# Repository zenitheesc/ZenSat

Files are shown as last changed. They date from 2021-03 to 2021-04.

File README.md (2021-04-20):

<h1 align="center" style="color:white; background-color:black">ZenSat</h1>
<h4 align="center">This is an Open Hardware and Software CubeSat developed by Zenith EESC-USP for the CubeDesign 2018.</h4>

<p align="center">
	<a href="http://zenith.eesc.usp.br/">
    
    </a>
    <a href="https://eesc.usp.br/">
    
    </a>
    <a href="https://github.com/zenitheesc/USPSat-AE1/blob/main/LICENSE">
    
    </a>
    <a href="https://github.com/zenitheesc/USPSat-AE1/issues">
    
    </a>
    <a href="https://github.com/zenitheesc/USPSat-AE1/commits/main">
    
    </a>
    <a href="https://github.com/zenitheesc/USPSat-AE1/graphs/contributors">
    
    </a>
    <a href="https://github.com/zenitheesc/USPSat-AE1/commits/main">
    
    </a>
    <a href="https://github.com/zenitheesc/USPSat-AE1/issues">
    
    </a>
    <a href="https://github.com/zenitheesc/USPSat-AE1/pulls">
    
    </a>
</p>

Aiming to participate in the first CubeDesign in 2018, Zenith designed its first nanosatellite prototype, which was named ”ZenSat”. This project was a 2U CubeSat for imaging missions in the competition. It is worth mentioning that the focus of the project was not to validate a nanosatellite for flight but to enable a first contact between the group members and the development of a nanosatellite.

<p align = "center">
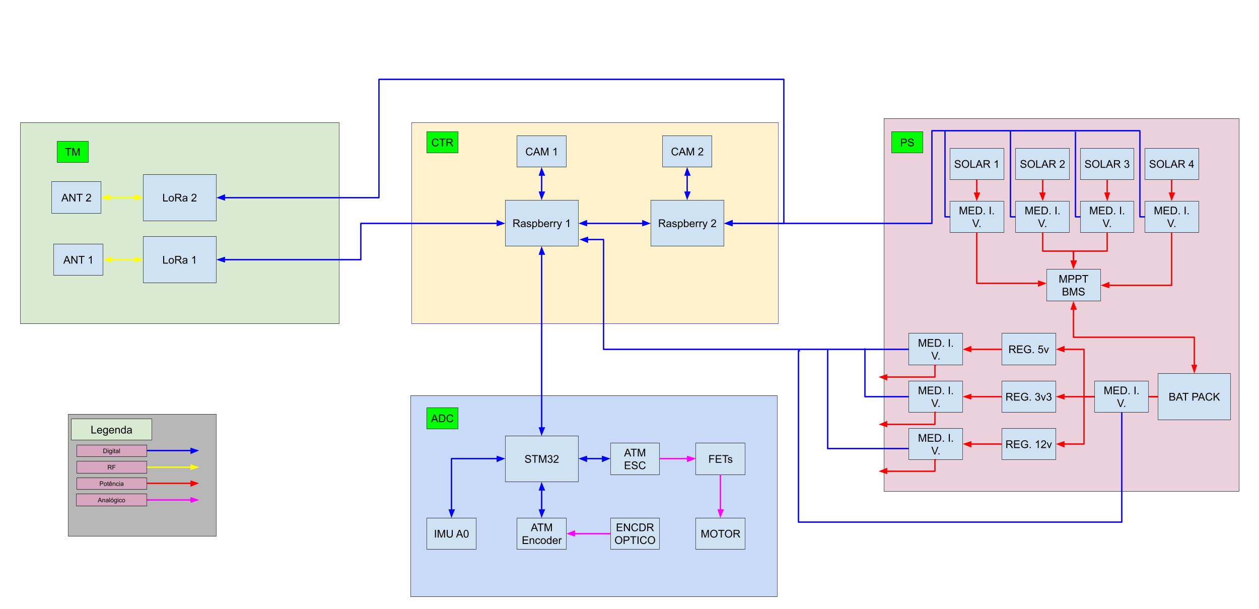
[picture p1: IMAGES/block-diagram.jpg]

</p>

<a href="https://github.com/zenitheesc/ZenSat_1.0/tree/master/ADC%20-%20Attitude%20Determination%20and%20Control"><h2> ADC - Attitude Determination and Control </h2></a>
The entire stabilization and pointing system must be done necessary to fulfill the competition missions. For this, the reading is done necessary sensors, activating a reaction wheel, which, by means of the Law of Conservation of Angular Momentum, manages to act in the attitude of the satellite.

<p align = "center">
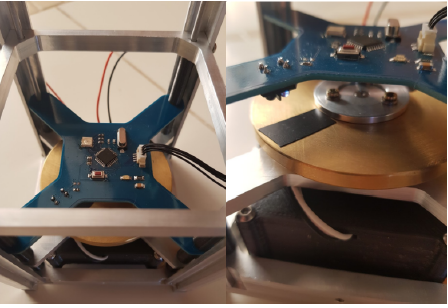
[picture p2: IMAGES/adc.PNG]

</p>

<a href="https://github.com/zenitheesc/ZenSat_1.0/tree/master/COM%20-%20Command%20and%20Telemetry"><h2>COM - Command and Telemetry</h2></a>
It is responsible by the bidirectional telemetry in cubesat. This System has two LoRa radios, which communicate with the CTRL Subsystem

<p align = "center">
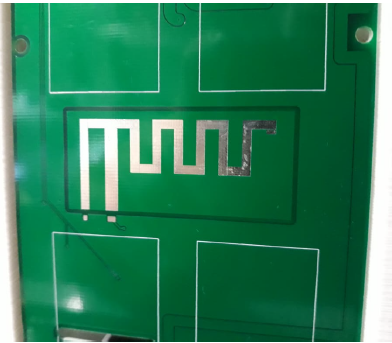
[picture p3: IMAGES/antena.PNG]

</p>

<a href="https://github.com/zenitheesc/ZenSat_1.0/tree/master/COM%20-%20Command%20and%20Telemetry"><h2>CTRL - Control</h2></a>
The Control System is the main component of the project. This system is responsible for data analysis, decision making and controlling the others systems
<p align = "center">
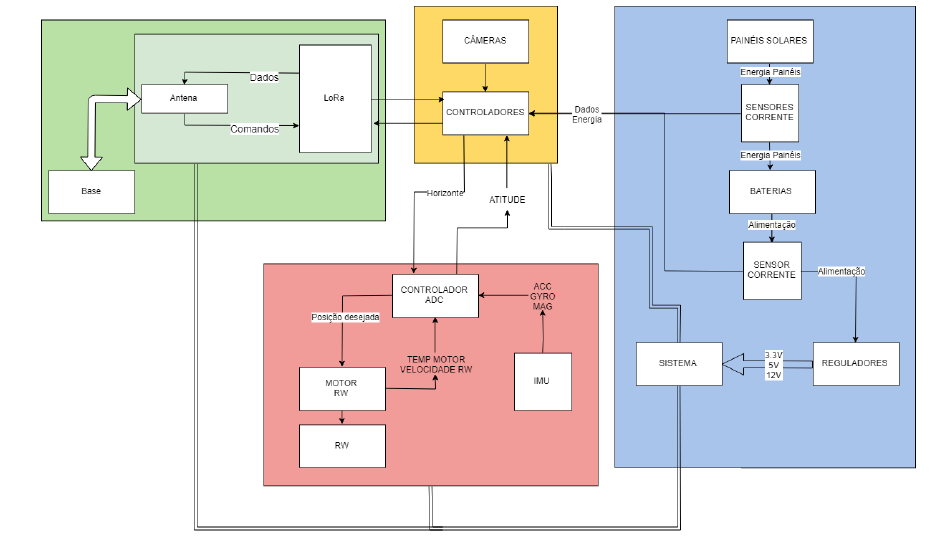
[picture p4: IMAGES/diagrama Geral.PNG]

</p>

<a href="https://github.com/zenitheesc/ZenSat_1.0/tree/master/PS%20-%20Power%20Supply"><h2>PS - Power Supply</h2></a>
Ensures the monitoring and control of EPS panel parameters,
that is, it performs the measurement of voltage and current levels at various points on the CubeSat;
monitors the temperature of the batteries and acts to keep it always positive, in addition to
carry out communication with other subsystems.
Also it performs conversions of battery voltage levels to the levels requested within the
hardware, making the necessary distribution, as well as controlling the loading of batteries through solar panels.

<p align = "center">
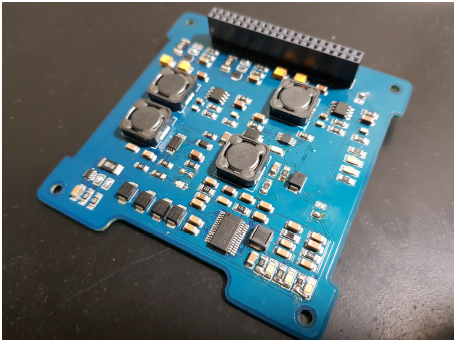
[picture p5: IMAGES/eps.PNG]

</p>

<a href="https://github.com/zenitheesc/ZenSat_1.0/tree/master/STT%20-%20Structure"><h2> STT - Structure </h2></a>
Finally, we have the subsystem responsible for the physical integration of all
the subsystems described earlier. All manufacturing issues involving
the physical structure of ZenSat is the responsibility of the structures subsystem. The
determination of the materials used, the choice of manufacturing processes and display of all components, aiming at a satisfactory performance in the
vibration, are the main focuses of this subsystem

<p align = "center">
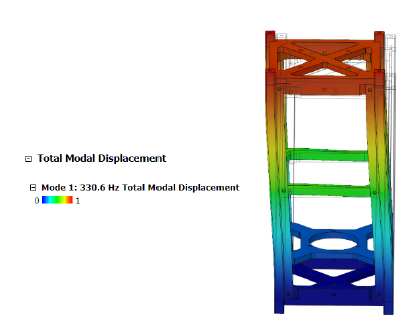
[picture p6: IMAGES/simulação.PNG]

</p>

## Official Documentation

Check out the official documentation [here](https://github.com/zenitheesc/ZenSat_1.0/blob/master/ZenSat%20v.1.0.pdf).

<p align = "center">
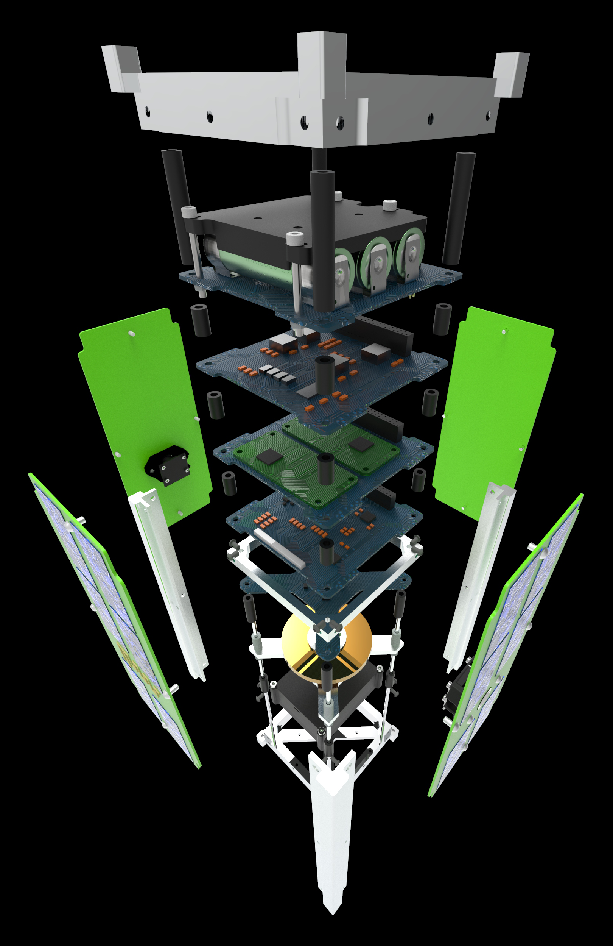
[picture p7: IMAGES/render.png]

</p>

<p align="center">
    <a href="http://zenith.eesc.usp.br">
    
    </a> 
    <a href="https://www.facebook.com/zenitheesc">
    
    </a> 
    <a href="https://www.instagram.com/zenith_eesc/">
    
    </a>

</p>
<p align = "center">
<a href="zenith.eesc@gmail.com">zenith.eesc@gmail.com</a>
</p>

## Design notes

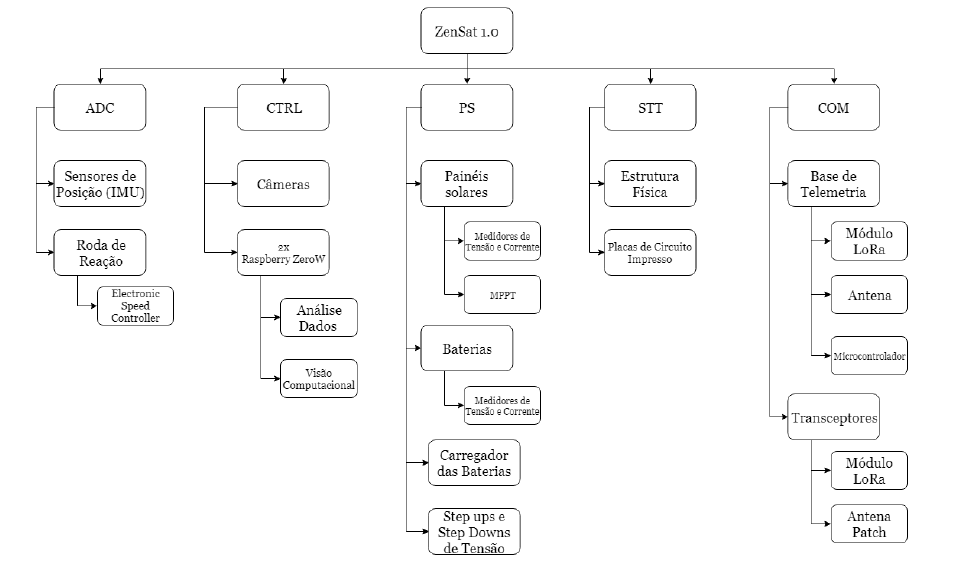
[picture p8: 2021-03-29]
IMAGES/breakdown.PNG

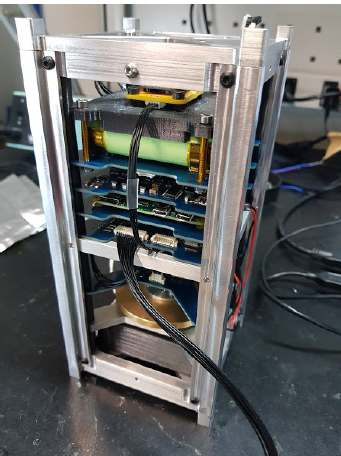
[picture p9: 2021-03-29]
IMAGES/aberto.PNG

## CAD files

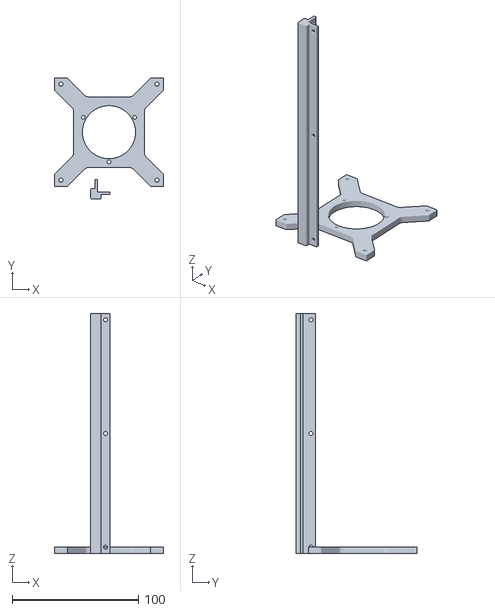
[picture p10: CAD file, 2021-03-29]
STT - Structure/trilho suporte motor.stl
86.0 x 96.0 x 190.0

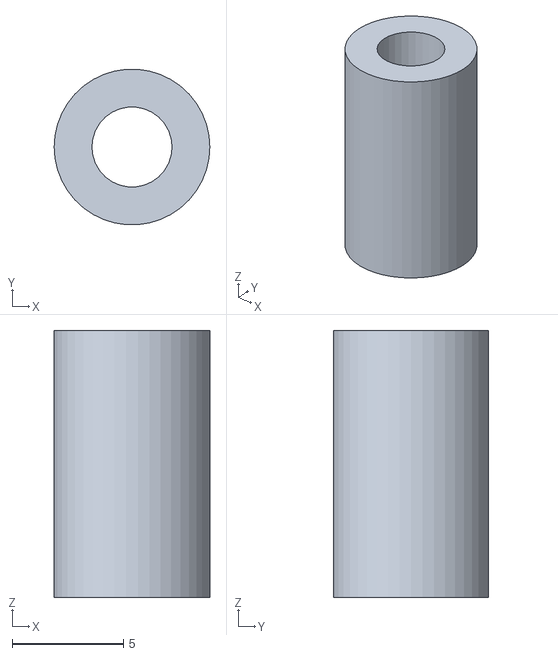
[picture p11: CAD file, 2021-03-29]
STT - Structure/espacador4.stl
7.00 x 6.98 x 12.0

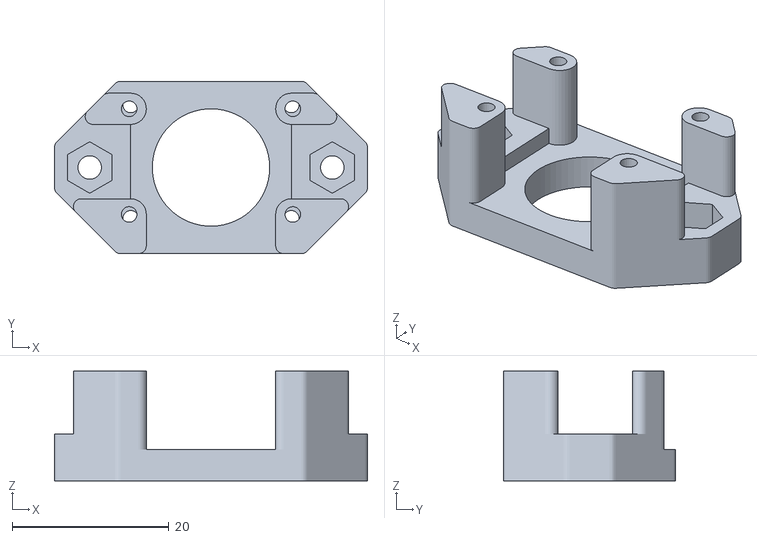
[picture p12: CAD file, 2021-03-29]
STT - Structure/suporte camera 2.0.stl
40.0 x 22.0 x 14.0

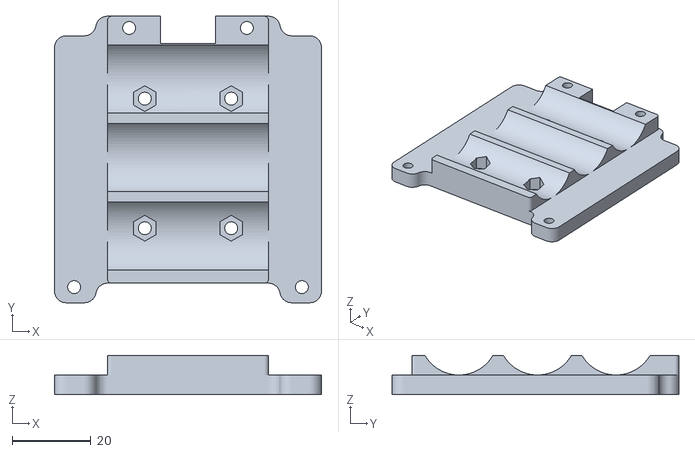
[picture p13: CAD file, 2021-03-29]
STT - Structure/suporte-baterias.stl
68.0 x 73.0 x 10.0

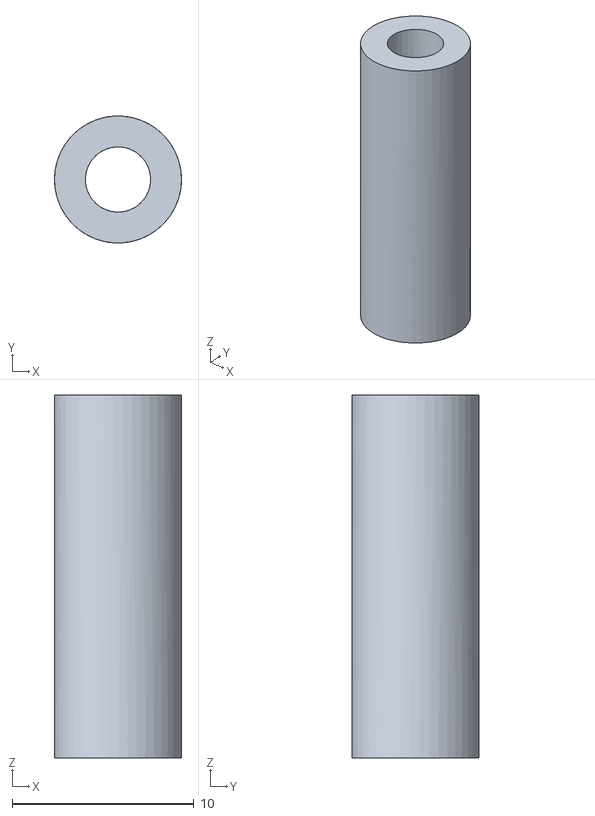
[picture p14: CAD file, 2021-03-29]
STT - Structure/espacador_1.stl
7.00 x 7.00 x 20.0

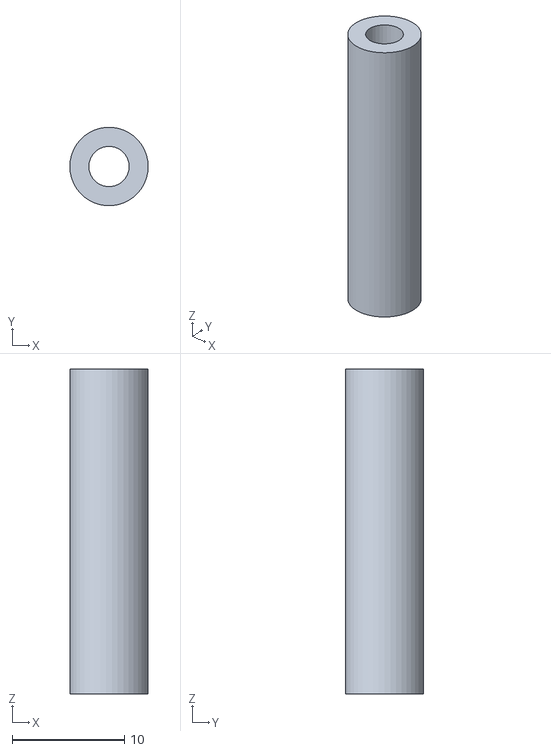
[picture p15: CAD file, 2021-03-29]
STT - Structure/espaçador3,6.stl
7.00 x 6.98 x 29.0

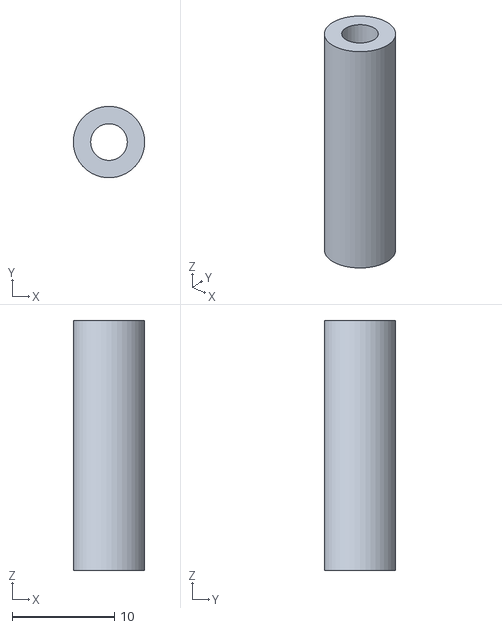
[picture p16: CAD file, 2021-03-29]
STT - Structure/espacador2.stl
7.00 x 6.99 x 24.5

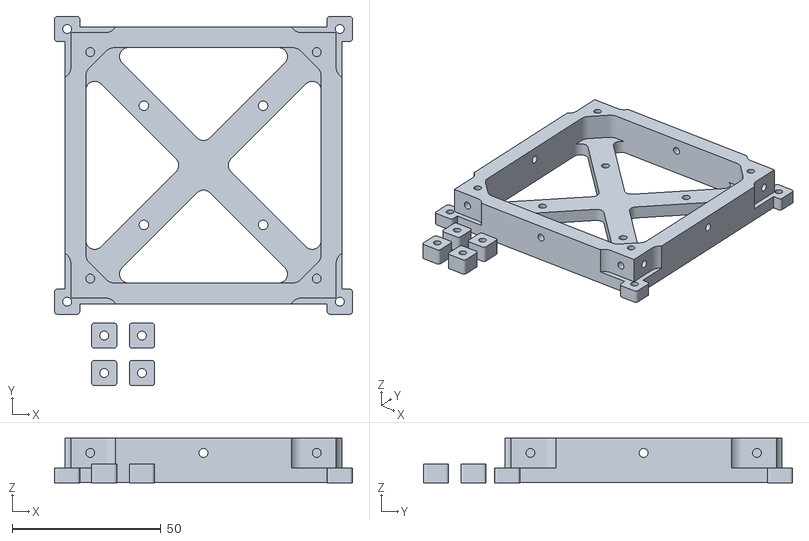
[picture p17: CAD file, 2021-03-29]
STT - Structure/tampa2_slice.stl
100.0 x 123.9 x 15.1

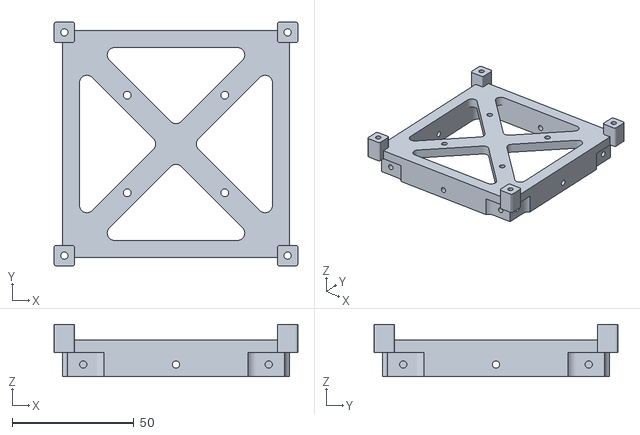
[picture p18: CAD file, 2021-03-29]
STT - Structure/tampa2.stl
100.0 x 100.0 x 21.5

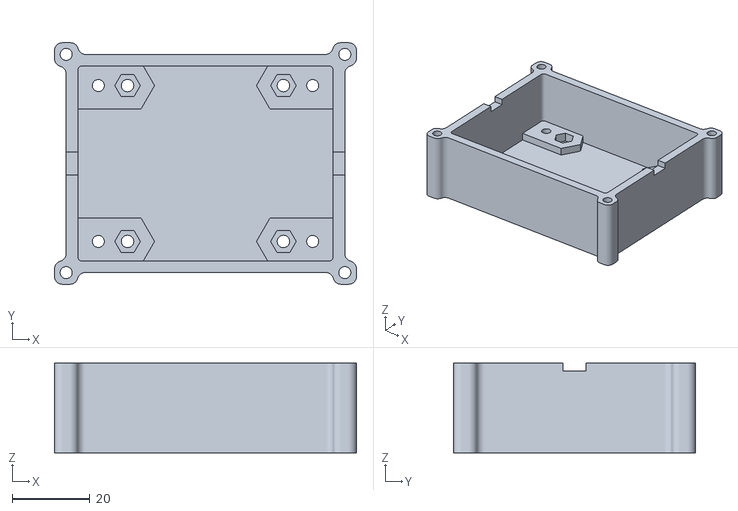
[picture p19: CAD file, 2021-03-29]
STT - Structure/caixa_esc.stl
77.5 x 62.0 x 23.0

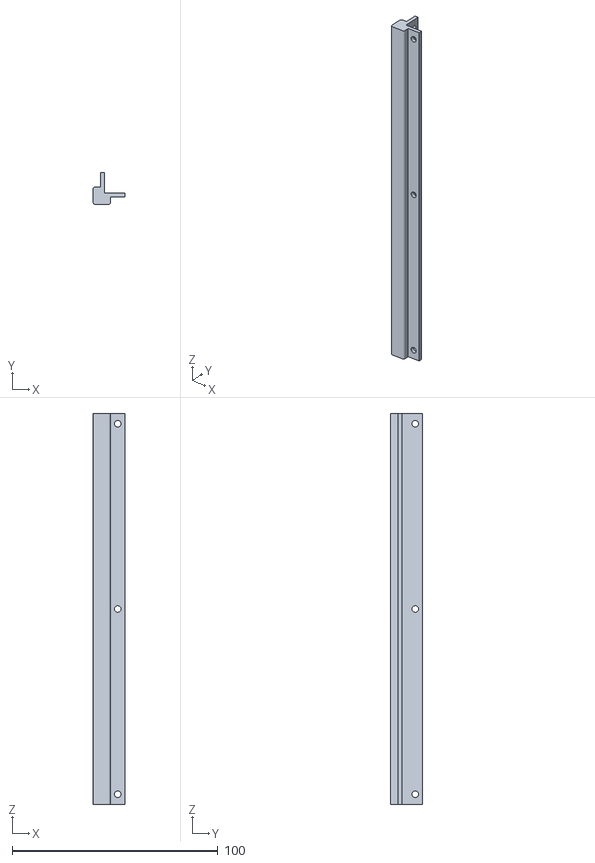
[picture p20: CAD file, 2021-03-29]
STT - Structure/trilho v2.0.stl
15.5 x 15.5 x 190.0

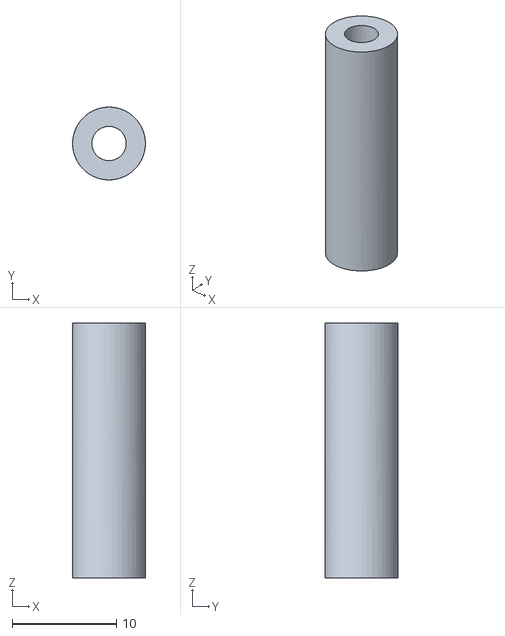
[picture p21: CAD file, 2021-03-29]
STT - Structure/espaçador_2.stl
7.00 x 7.00 x 24.5

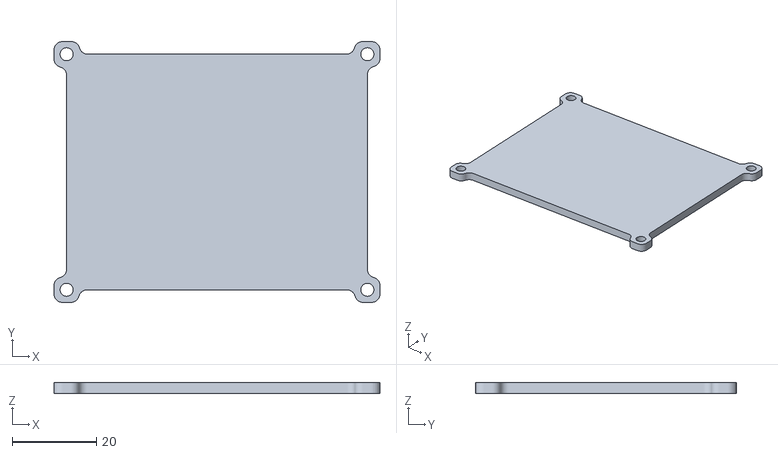
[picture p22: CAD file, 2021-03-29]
STT - Structure/tampa_esc.stl
77.5 x 62.0 x 2.50

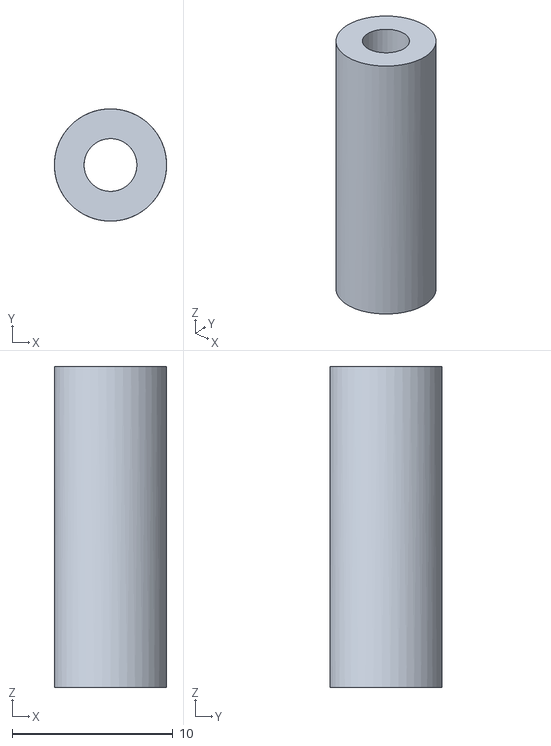
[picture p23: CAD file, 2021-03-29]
STT - Structure/espaçador_1.stl
7.00 x 7.00 x 20.0

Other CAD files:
STT - Structure/espacador 3.stl
STT - Structure/espacador5.stl
STT - Structure/suporte roda.stl

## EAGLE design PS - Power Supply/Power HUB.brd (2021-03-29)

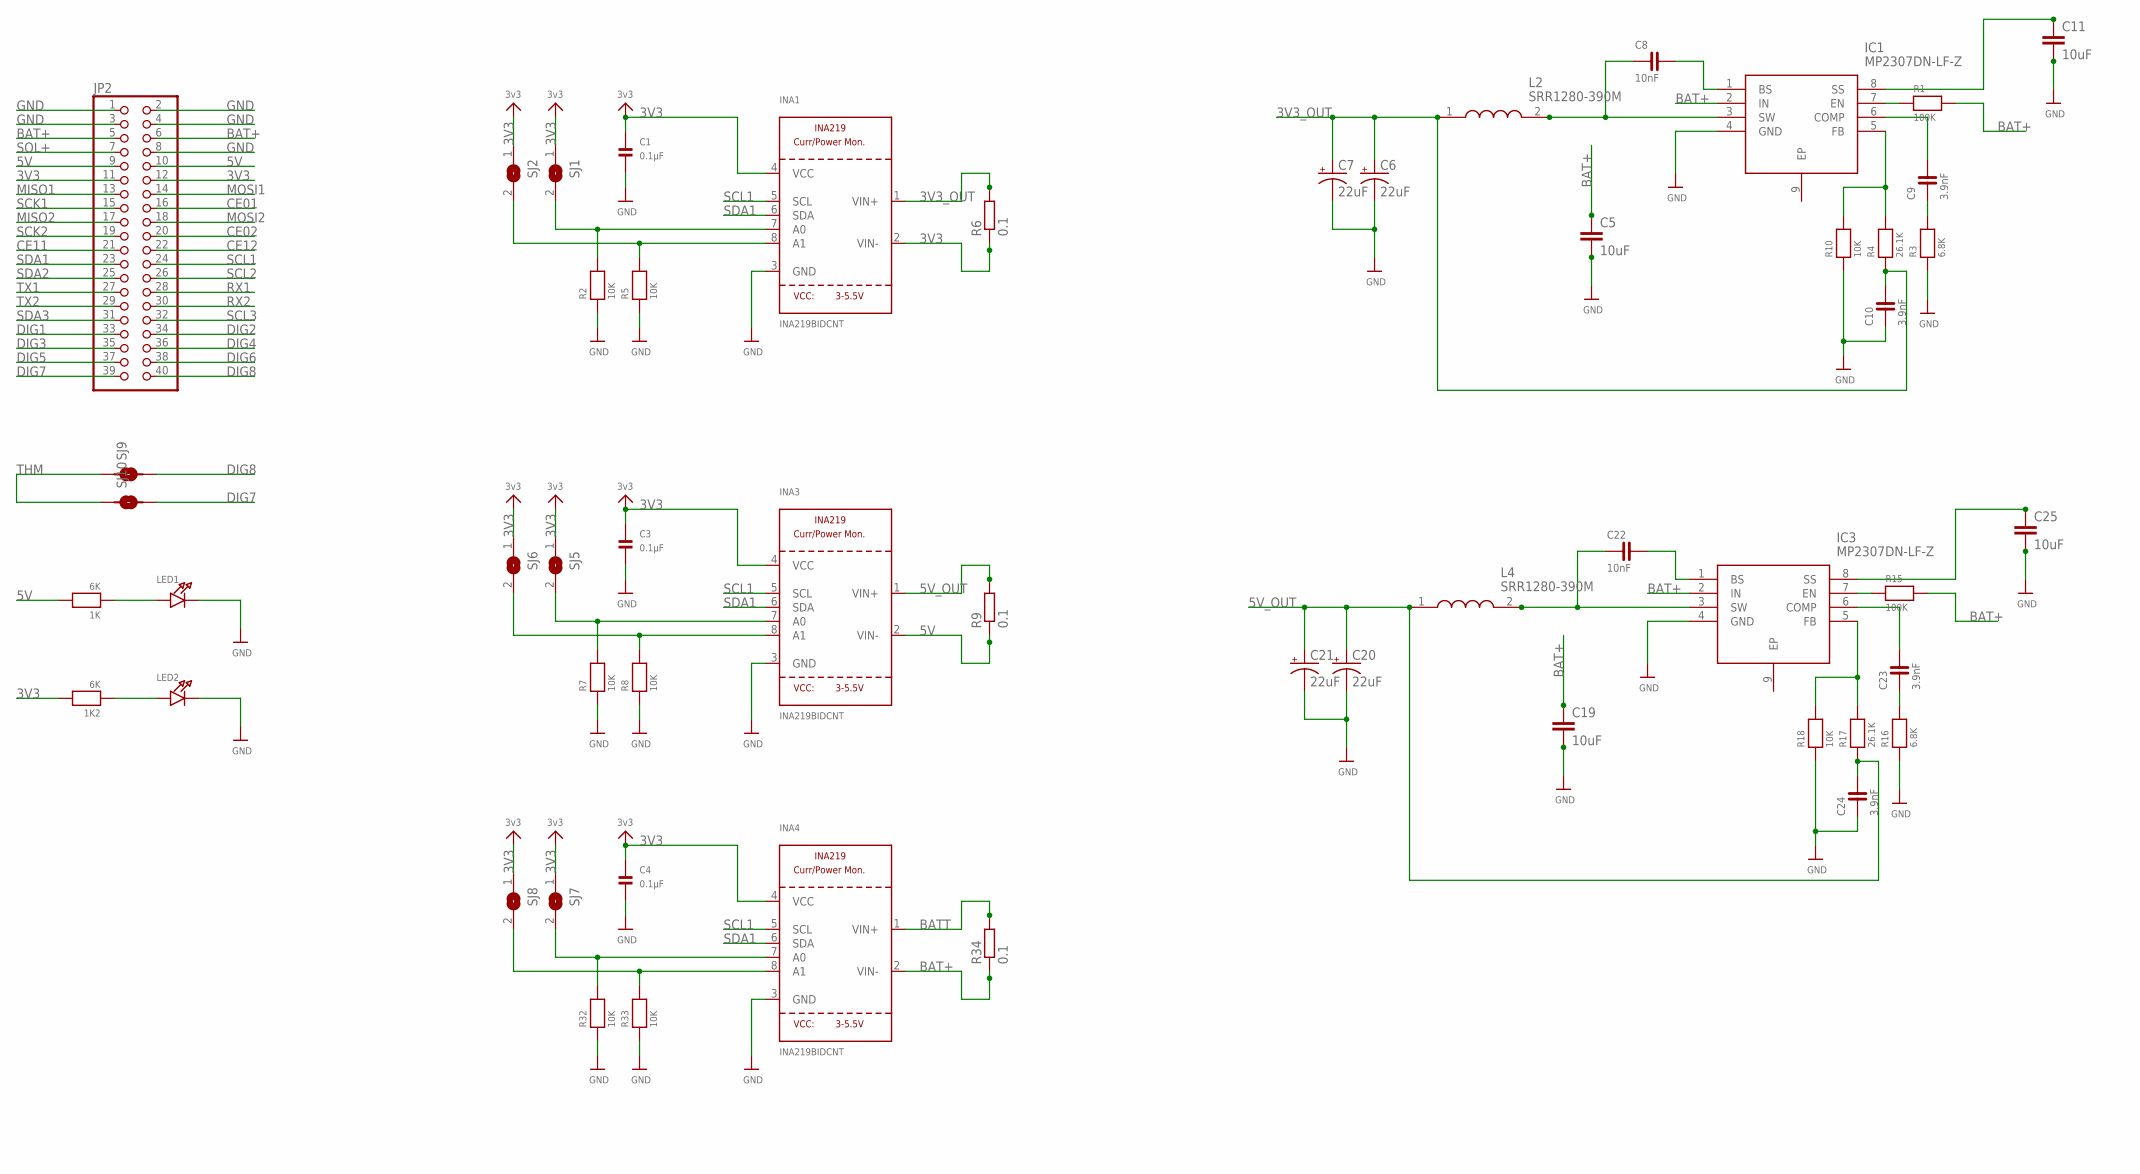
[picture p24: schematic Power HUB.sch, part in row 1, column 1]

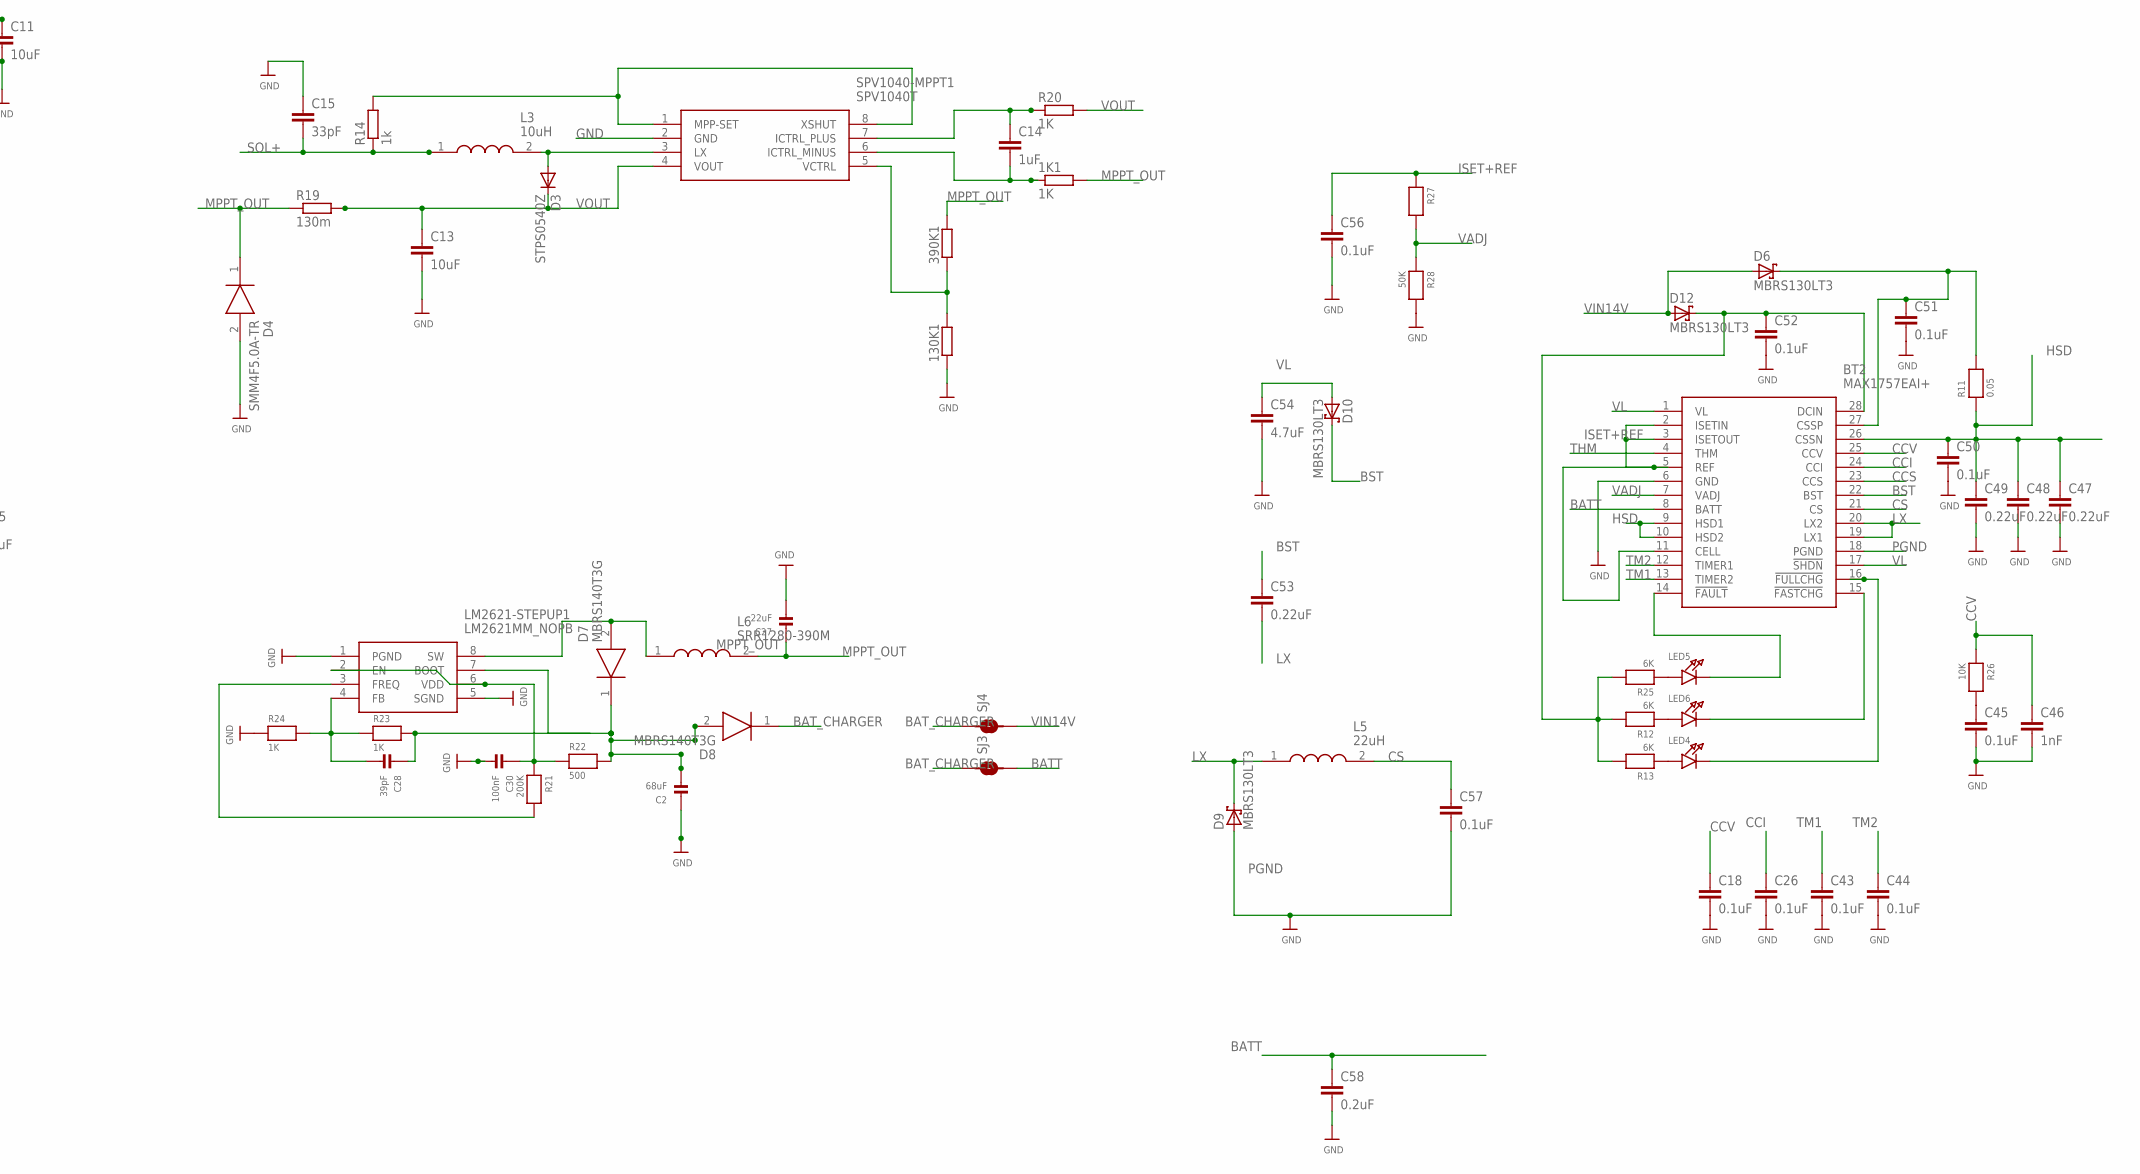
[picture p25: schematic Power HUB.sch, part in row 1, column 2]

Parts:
1K, 1K2: 6K; 1206
1K1: 1K; R1206
130K1, 390K1: RR1206; R1206
BT2: MAX1757EAI+; SOP65P778X199-28N
C1, C3, C4: 0.1µF; 1206
C2: 68uF; 1206
C5, C11, C13, C19, C25: 10uF; C1206
C6, C7, C20, C21: 22uF; EIA3528
C8, C22: 10nF; 0805
C9, C10, C23, C24: 3.9nF; 0805
C14: 1uF; C1206
C15: 33pF; C1206
C18, C26, C43, C44, C45, C50, C51, C52, C56, C57: 0.1uF; C1206
C27: 22uF; 1206
C28: 39pF; 1206
C30: 100nF; 1206
C46: 1nF; C1206
C47, C48, C49, C53: 0.22uF; C1206
C54: 4.7uF; C1206
C58: 0.2uF; C1206
D3: STPS0540Z; SOD-123_MINI-SMA
D4: SMM4F5.0A-TR; STMITE
D6, D9, D10, D12: MBRS130LT3; SMB
D7, D8: MBRS140T3G; DIOM5436X247N
IC1, IC3: MP2307DN-LF-Z; SOIC127P600X170-9N
INA1, INA3, INA4: INA219BIDCNT; SOT23-8
JP2: PINHD-2X20; 2X20
L2, L4, L6: SRR1280-390M; SRR1280-220M
L3: 10uH; SRR1280-220M
L5: 22uH; INDPM4848X280N
LED1, LED2, LED4, LED5, LED6: LED1206; CHIPLED_1206
LM2621-STEPUP1: LM2621MM_NOPB; SOP65P490X110-8N
R1, R15: 100K; 1206
R2, R5, R7, R8, R10, R18, R26, R32, R33: 10K; 1206
R3, R16: 6.8K; 1206
R4, R17: 26.1K; 1206
R6, R9, R34: 0.1; R2512
R11: 0.05; 1206
R12, R13, R25: 6K; 1206
R14: 1k; R1206
R19: 130m; R1206
R20: 1K; R1206
R21: 200K; 1206
R22: 500; 1206
R23, R24: 1K; 1206
R27: RESISTOR1206; 1206
R28: 50K; 1206
SJ1, SJ2, SJ5, SJ6, SJ7, SJ8: SOLDERJUMPERREFLOW_NOPASTE; SOLDERJUMPER_REFLOW_NOPASTE
SJ3, SJ4, SJ9, SJ10: SMD-JUMPER-2
SPV1040-MPPT1: SPV1040T; SOP65P640X120-8N

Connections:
3V3: 1K2.2, C1.1, C3.1, C4.1, INA1.2 (VIN-), INA1.4 (VCC), INA3.4 (VCC), INA4.4 (VCC), JP2.11, JP2.12, R6.1, SJ1.1, SJ2.1, SJ5.1, SJ6.1, SJ7.1, SJ8.1
3V3_OUT: C6.A (+), C7.A (+), C10.2, INA1.1 (VIN+), L2.1, R4.1, R6.2
5V: 1K.2, INA3.2 (VIN-), JP2.9, JP2.10, R9.1
5V_OUT: C20.A (+), C21.A (+), C24.2, INA3.1 (VIN+), L4.1, R9.2, R17.1
BAT+: C5.1, C19.1, IC1.2 (IN), IC3.2 (IN), INA4.2 (VIN-), JP2.5, JP2.6, R1.2, R15.2, R34.1
BATT: BT2.8 (BATT), C58.1, INA4.1 (VIN+), R34.2, SJ3.2
BAT_CHARGER: D8.1 (K), SJ3.1, SJ4.1
BST: BT2.22 (BST), C53.1, D10.C
CCI: BT2.24 (CCI), C26.1
CCS: BT2.23 (CCS)
CCV: BT2.25 (CCV), C18.1, C46.1, R26.1
CE01: JP2.16
CE02: JP2.20
CE11: JP2.21
CE12: JP2.22
CS: BT2.21 (CS), C57.1, L5.2
DIG1: JP2.33
DIG2: JP2.34
DIG3: JP2.35
DIG4: JP2.36
DIG5: JP2.37
DIG6: JP2.38
DIG7: JP2.39, SJ10.2
DIG8: JP2.40, SJ9.2
GND: 130K1.1, BT2.6 (GND), C1.2, C2.1, C3.2, C4.2, C5.2, C6.C (-), C7.C (-), C10.1, C11.2, C13.2, C15.1, C19.2, C20.C (-), C21.C (-), C24.1, C25.2, C27.2, C30.2, C45.2, C46.2, C47.2, C48.2, C49.2, C54.2, C56.2, C58.2, D4.2 (A), IC1.4 (GND), IC3.4 (GND), INA1.3 (GND), INA3.3 (GND), INA4.3 (GND), JP2.1, JP2.2, JP2.3, JP2.4, JP2.8, LED1.C, LED2.C, LM2621-STEPUP1.1 (PGND), LM2621-STEPUP1.5 (SGND), R2.1, R3.1, R5.1, R7.1, R8.1, R10.1, R16.1, R18.1, R24.1, R32.1, R33.1, SPV1040-MPPT1.2 (GND)
HSD: BT2.9 (HSD1), BT2.10 (HSD2), BT2.26 (CSSN), C47.1, C48.1, C49.1, C50.1, R11.1
ISET+REF: BT2.2 (ISETIN), BT2.3 (ISETOUT), BT2.5 (REF), BT2.11 (CELL), C56.1, R27.1
LX: BT2.19 (LX1), BT2.20 (LX2), C53.2, D9.C, L5.1
MISO1: JP2.13
MISO2: JP2.17
MOSI1: JP2.14
MOSI2: JP2.18
MPPT_OUT: 1K1.2, 390K1.2, C27.1, D4.1 (K), L6.2, R19.1
unnamed: INA1.8 (A1), R5.2, SJ2.2
unnamed: INA1.7 (A0), R2.2, SJ1.2
unnamed: C8.2, IC1.1 (BS)
unnamed: C11.1, IC1.8 (SS)
unnamed: INA3.8 (A1), R8.2, SJ6.2
unnamed: INA3.7 (A0), R7.2, SJ5.2
unnamed: C8.1, IC1.3 (SW), L2.2
unnamed: IC1.7 (EN), R1.1
unnamed: C9.2, IC1.6 (COMP)
unnamed: C9.1, R3.2
unnamed: IC1.5 (FB), R4.2, R10.2
unnamed: 1K2.1, LED2.A
unnamed: 1K.1, LED1.A
unnamed: BT2.28 (DCIN), C52.1, D12.C, R12.2, R13.2, R25.2
unnamed: BT2.14 (!FAULT), LED5.C
unnamed: D3.A, L3.2, SPV1040-MPPT1.3 (LX)
unnamed: R14.2, SPV1040-MPPT1.1 (MPP-SET), SPV1040-MPPT1.8 (XSHUT)
unnamed: C22.2, IC3.1 (BS)
unnamed: C25.1, IC3.8 (SS)
unnamed: C22.1, IC3.3 (SW), L4.2
unnamed: IC3.7 (EN), R15.1
unnamed: C23.2, IC3.6 (COMP)
unnamed: C23.1, R16.2
unnamed: IC3.5 (FB), R17.2, R18.2
unnamed: C14.1, R20.1, SPV1040-MPPT1.7 (ICTRL_PLUS)
unnamed: 1K1.1, C14.2, SPV1040-MPPT1.6 (ICTRL_MINUS)
unnamed: 130K1.2, 390K1.1, SPV1040-MPPT1.5 (VCTRL)
unnamed: BT2.15 (!FASTCHG), LED6.C
unnamed: BT2.16 (!FULLCHG), LED4.C
unnamed: INA4.8 (A1), R33.2, SJ8.2
unnamed: C2.2, D7.1 (K), D8.2 (A), LM2621-STEPUP1.7 (BOOT), R22.2
unnamed: C30.1, LM2621-STEPUP1.2 (EN), LM2621-STEPUP1.6 (VDD), R21.1, R22.1
unnamed: LM2621-STEPUP1.3 (FREQ), R21.2
unnamed: C28.2, LM2621-STEPUP1.4 (FB), R23.1, R24.2
unnamed: C28.1, R23.2
unnamed: D7.2 (A), L6.1, LM2621-STEPUP1.8 (SW)
unnamed: INA4.7 (A0), R32.2, SJ7.2
unnamed: BT2.27 (CSSP), C51.1, D6.C, R11.2
PGND: BT2.18 (PGND), C57.2, D9.A
RX1: JP2.28
RX2: JP2.30
SCK1: JP2.15
SCK2: JP2.19
SCL1: INA1.5 (SCL), INA3.5 (SCL), INA4.5 (SCL), JP2.24
SCL2: JP2.26
SCL3: JP2.32
SDA1: INA1.6 (SDA), INA3.6 (SDA), INA4.6 (SDA), JP2.23
SDA2: JP2.25
SDA3: JP2.31
SOL+: C15.2, JP2.7, L3.1, R14.1
THM: BT2.4 (THM), SJ9.1, SJ10.1
TM1: BT2.13 (TIMER2), C43.1
TM2: BT2.12 (TIMER1), C44.1
TX1: JP2.27
TX2: JP2.29
VADJ: BT2.7 (VADJ), R27.2, R28.1
VIN14V: D6.A, D12.A, SJ4.2
VL: BT2.1 (VL), BT2.17 (!SHDN), C54.1, D10.A
VOUT: C13.1, D3.C, R19.2, R20.2, SPV1040-MPPT1.4 (VOUT)

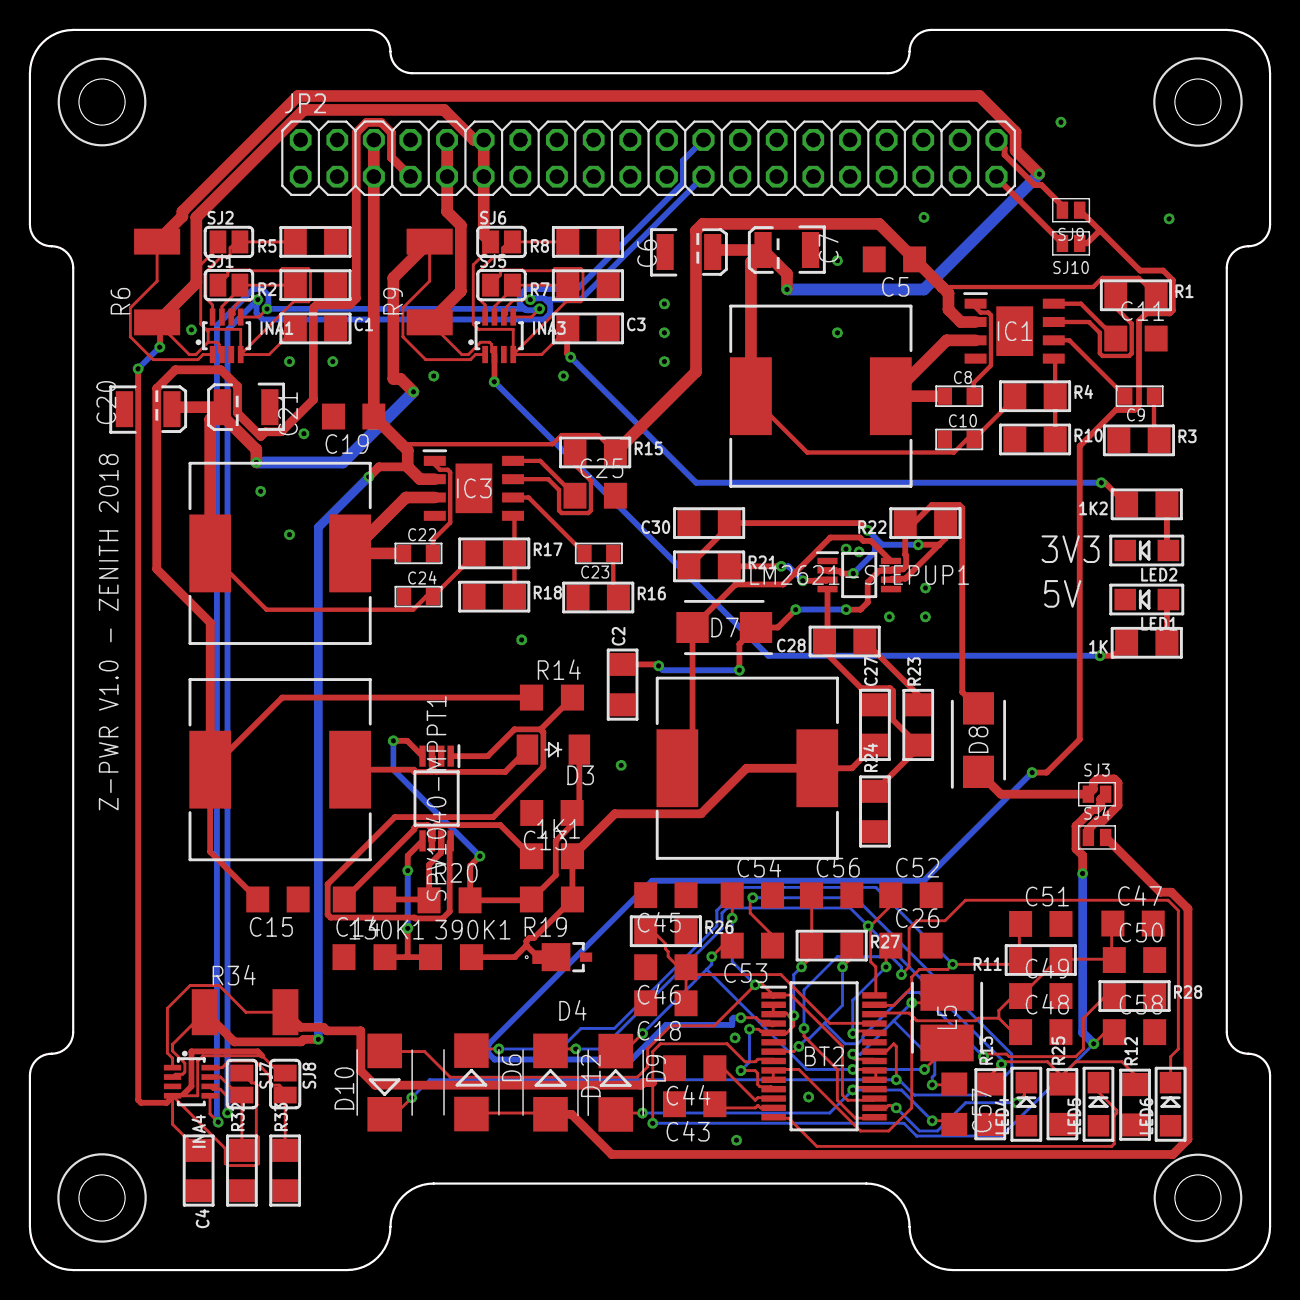
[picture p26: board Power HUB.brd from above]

Board: 2 copper layers, 86.0 x 86.0 mm, 114 parts (0 on the bottom side), 67 nets.

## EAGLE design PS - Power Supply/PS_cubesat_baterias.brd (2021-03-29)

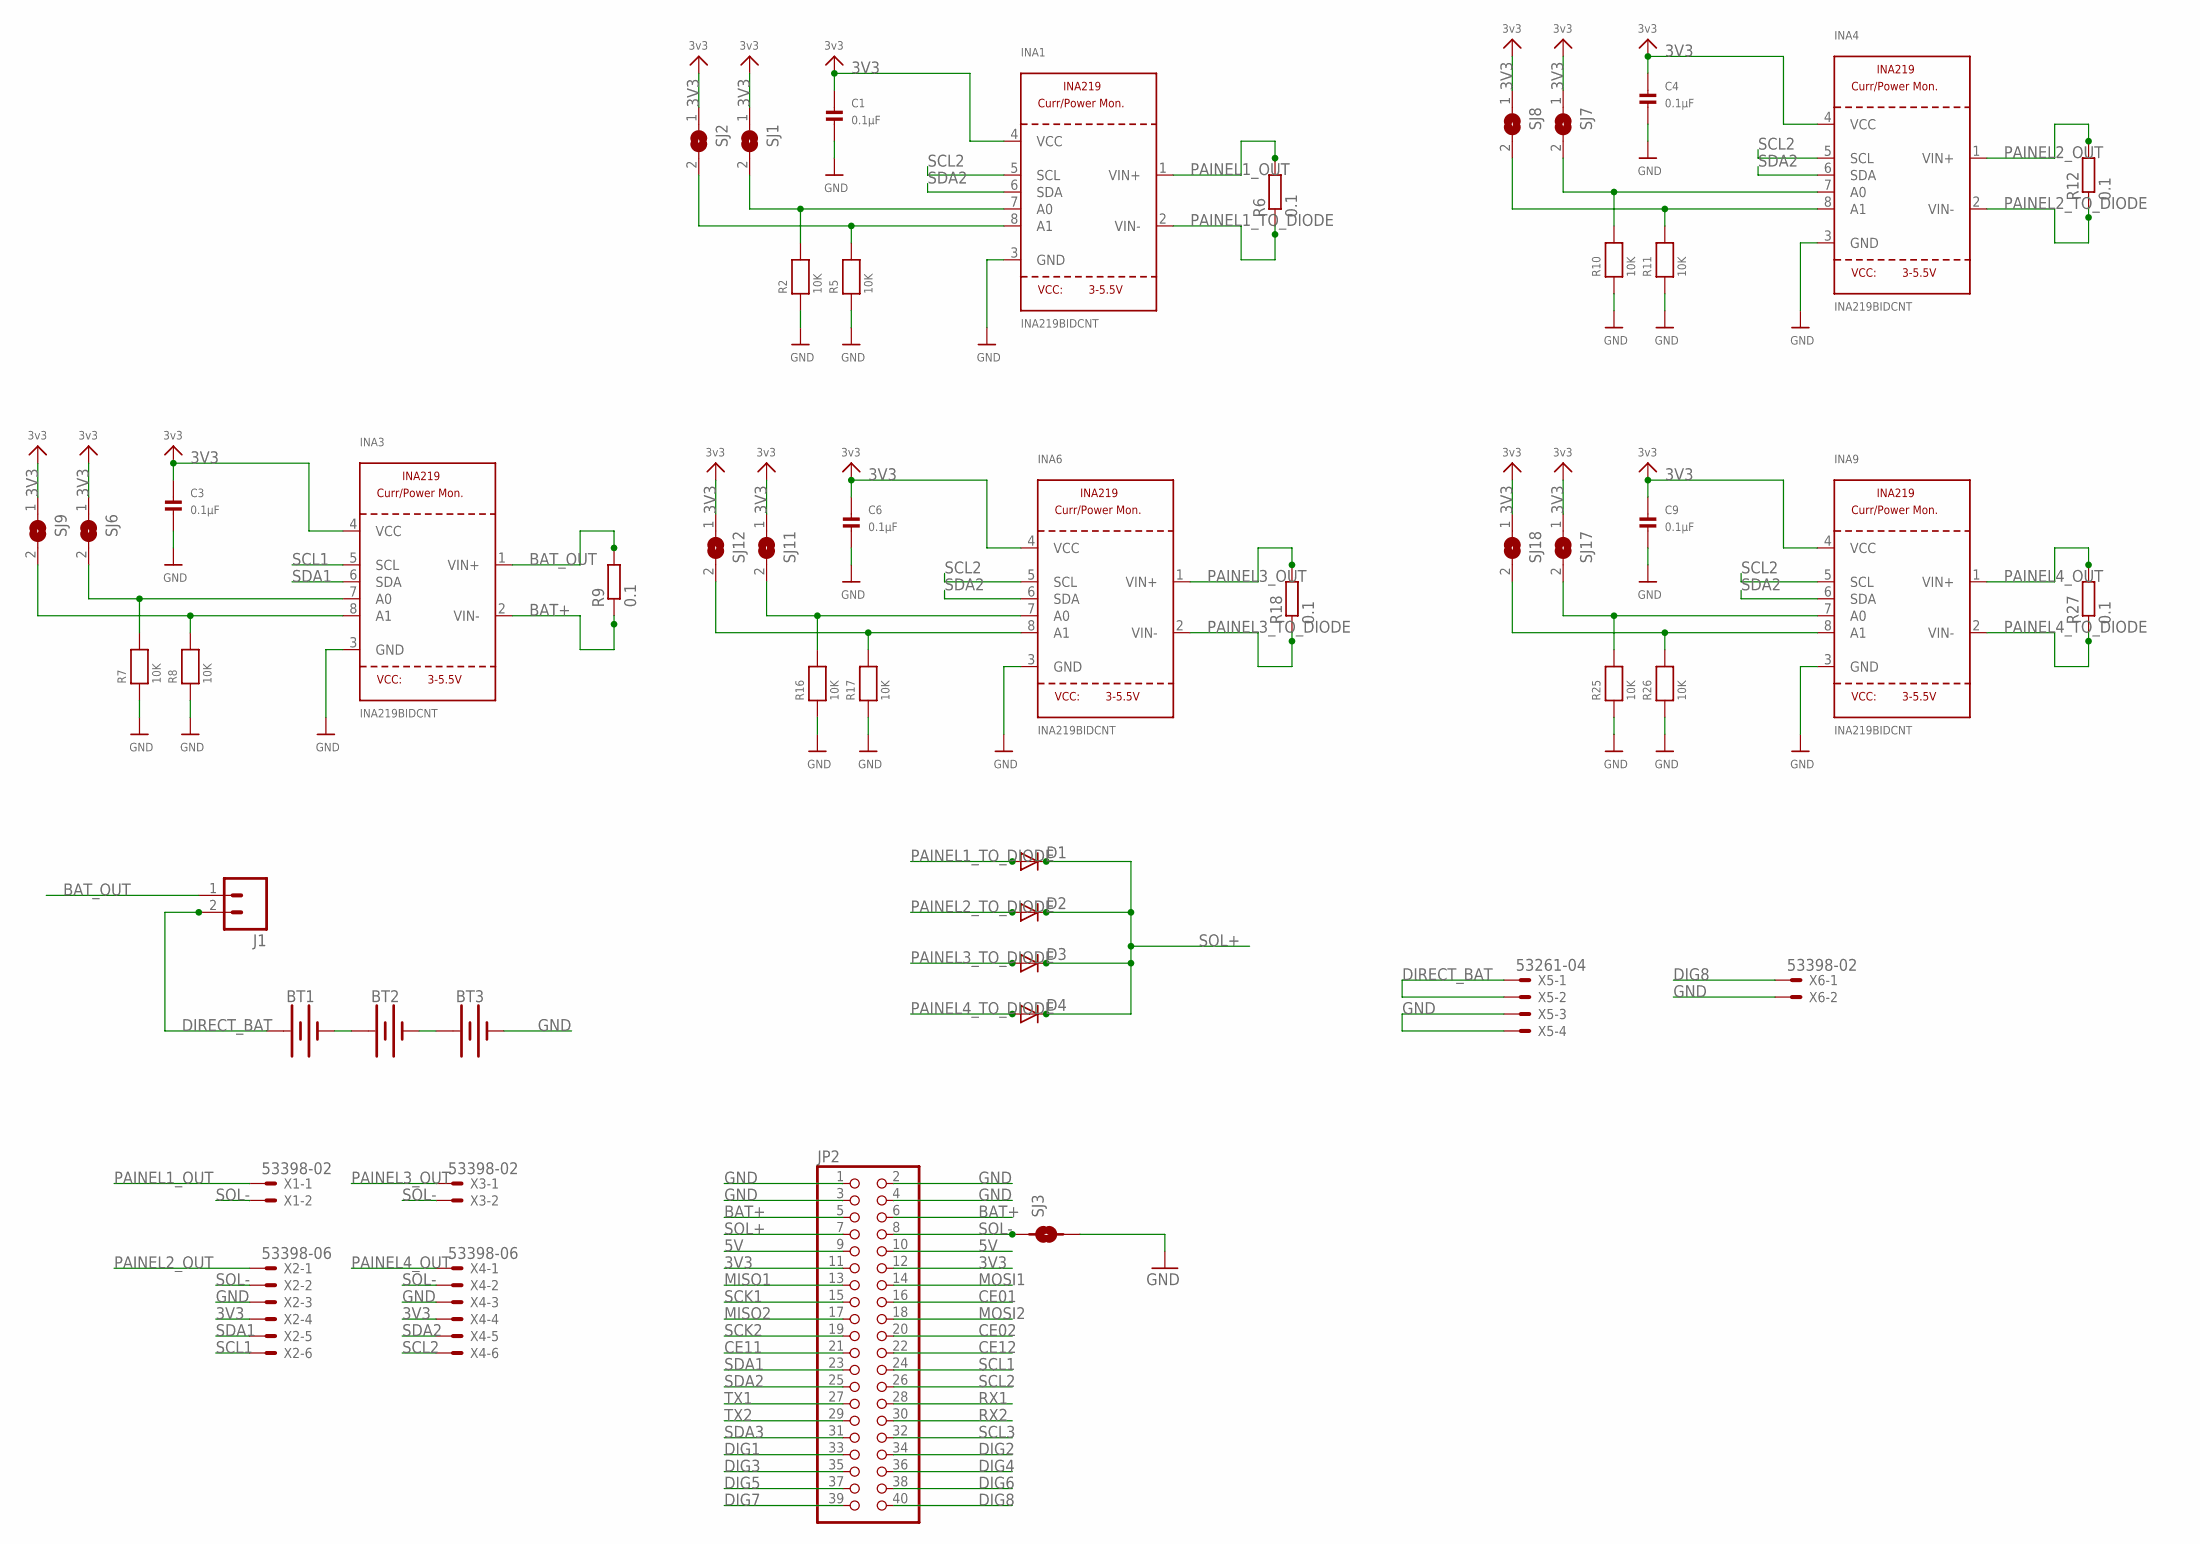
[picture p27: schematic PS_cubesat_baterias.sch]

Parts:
BT1, BT2, BT3: BATTERY-18650; BATTERY_18650-HOLDER
C1, C3, C4, C6, C9: 0.1µF; 1206
D1, D2, D3, D4: DIODE-DO-214AC; DO-214AC
INA1, INA3, INA4, INA6, INA9: INA219BIDCNT; SOT23-8
J1: M02JST-PTH-VERT; JST-2-PTH-VERT
JP2: PINHD-2X20; 2X20
R2, R5, R7, R8, R10, R11, R16, R17, R25, R26: 10K; 1206
R6, R9, R12, R18, R27: 0.1; R2512
SJ1, SJ2, SJ6, SJ7, SJ8, SJ9, SJ11, SJ12, SJ17, SJ18: SOLDERJUMPERREFLOW_NOPASTE; SOLDERJUMPER_REFLOW_NOPASTE
SJ3: SMD-JUMPER-2
X1, X3, X6: 53398-02
X2, X4: 53398-06
X5: 53261-04

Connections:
3V3: C1.1, C3.1, C4.1, C6.1, C9.1, INA1.4 (VCC), INA3.4 (VCC), INA4.4 (VCC), INA6.4 (VCC), INA9.4 (VCC), JP2.11, JP2.12, SJ1.1, SJ2.1, SJ6.1, SJ7.1, SJ8.1, SJ9.1, SJ11.1, SJ12.1, SJ17.1, SJ18.1, X2.4, X4.4
5V: JP2.9, JP2.10
BAT+: INA3.2 (VIN-), JP2.5, JP2.6, R9.1
BAT_OUT: INA3.1 (VIN+), J1.1, R9.2
CE01: JP2.16
CE02: JP2.20
CE11: JP2.21
CE12: JP2.22
DIG1: JP2.33
DIG2: JP2.34
DIG3: JP2.35
DIG4: JP2.36
DIG5: JP2.37
DIG6: JP2.38
DIG7: JP2.39
DIG8: JP2.40, X6.1
DIRECT_BAT: BT1.PWR@1 (+), J1.2, X5.1, X5.2
GND: BT3.GND@1 (-), C1.2, C3.2, C4.2, C6.2, C9.2, INA1.3 (GND), INA3.3 (GND), INA4.3 (GND), INA6.3 (GND), INA9.3 (GND), JP2.1, JP2.2, JP2.3, JP2.4, R2.1, R5.1, R7.1, R8.1, R10.1, R11.1, R16.1, R17.1, R25.1, R26.1, SJ3.2, X2.3, X4.3, X5.3, X5.4, X6.2
MISO1: JP2.13
MISO2: JP2.17
MOSI1: JP2.14
MOSI2: JP2.18
unnamed: BT1.GND@1 (-), BT2.PWR@1 (+)
unnamed: BT2.GND@1 (-), BT3.PWR@1 (+)
unnamed: INA1.8 (A1), R5.2, SJ2.2
unnamed: INA1.7 (A0), R2.2, SJ1.2
unnamed: INA3.8 (A1), R8.2, SJ9.2
unnamed: INA3.7 (A0), R7.2, SJ6.2
unnamed: INA4.8 (A1), R11.2, SJ8.2
unnamed: INA4.7 (A0), R10.2, SJ7.2
unnamed: INA6.8 (A1), R17.2, SJ12.2
unnamed: INA6.7 (A0), R16.2, SJ11.2
unnamed: INA9.8 (A1), R26.2, SJ18.2
unnamed: INA9.7 (A0), R25.2, SJ17.2
PAINEL1_OUT: INA1.1 (VIN+), R6.2, X1.1
PAINEL1_TO_DIODE: D1.A, INA1.2 (VIN-), R6.1
PAINEL2_OUT: INA4.1 (VIN+), R12.2, X2.1
PAINEL2_TO_DIODE: D2.A, INA4.2 (VIN-), R12.1
PAINEL3_OUT: INA6.1 (VIN+), R18.2, X3.1
PAINEL3_TO_DIODE: D3.A, INA6.2 (VIN-), R18.1
PAINEL4_OUT: INA9.1 (VIN+), R27.2, X4.1
PAINEL4_TO_DIODE: D4.A, INA9.2 (VIN-), R27.1
RX1: JP2.28
RX2: JP2.30
SCK1: JP2.15
SCK2: JP2.19
SCL1: INA3.5 (SCL), JP2.24, X2.6
SCL2: INA1.5 (SCL), INA4.5 (SCL), INA6.5 (SCL), INA9.5 (SCL), JP2.26, X4.6
SCL3: JP2.32
SDA1: INA3.6 (SDA), JP2.23, X2.5
SDA2: INA1.6 (SDA), INA4.6 (SDA), INA6.6 (SDA), INA9.6 (SDA), JP2.25, X4.5
SDA3: JP2.31
SOL+: D1.C, D2.C, D3.C, D4.C, JP2.7
SOL-: JP2.8, SJ3.1, X1.2, X2.2, X3.2, X4.2
TX1: JP2.27
TX2: JP2.29

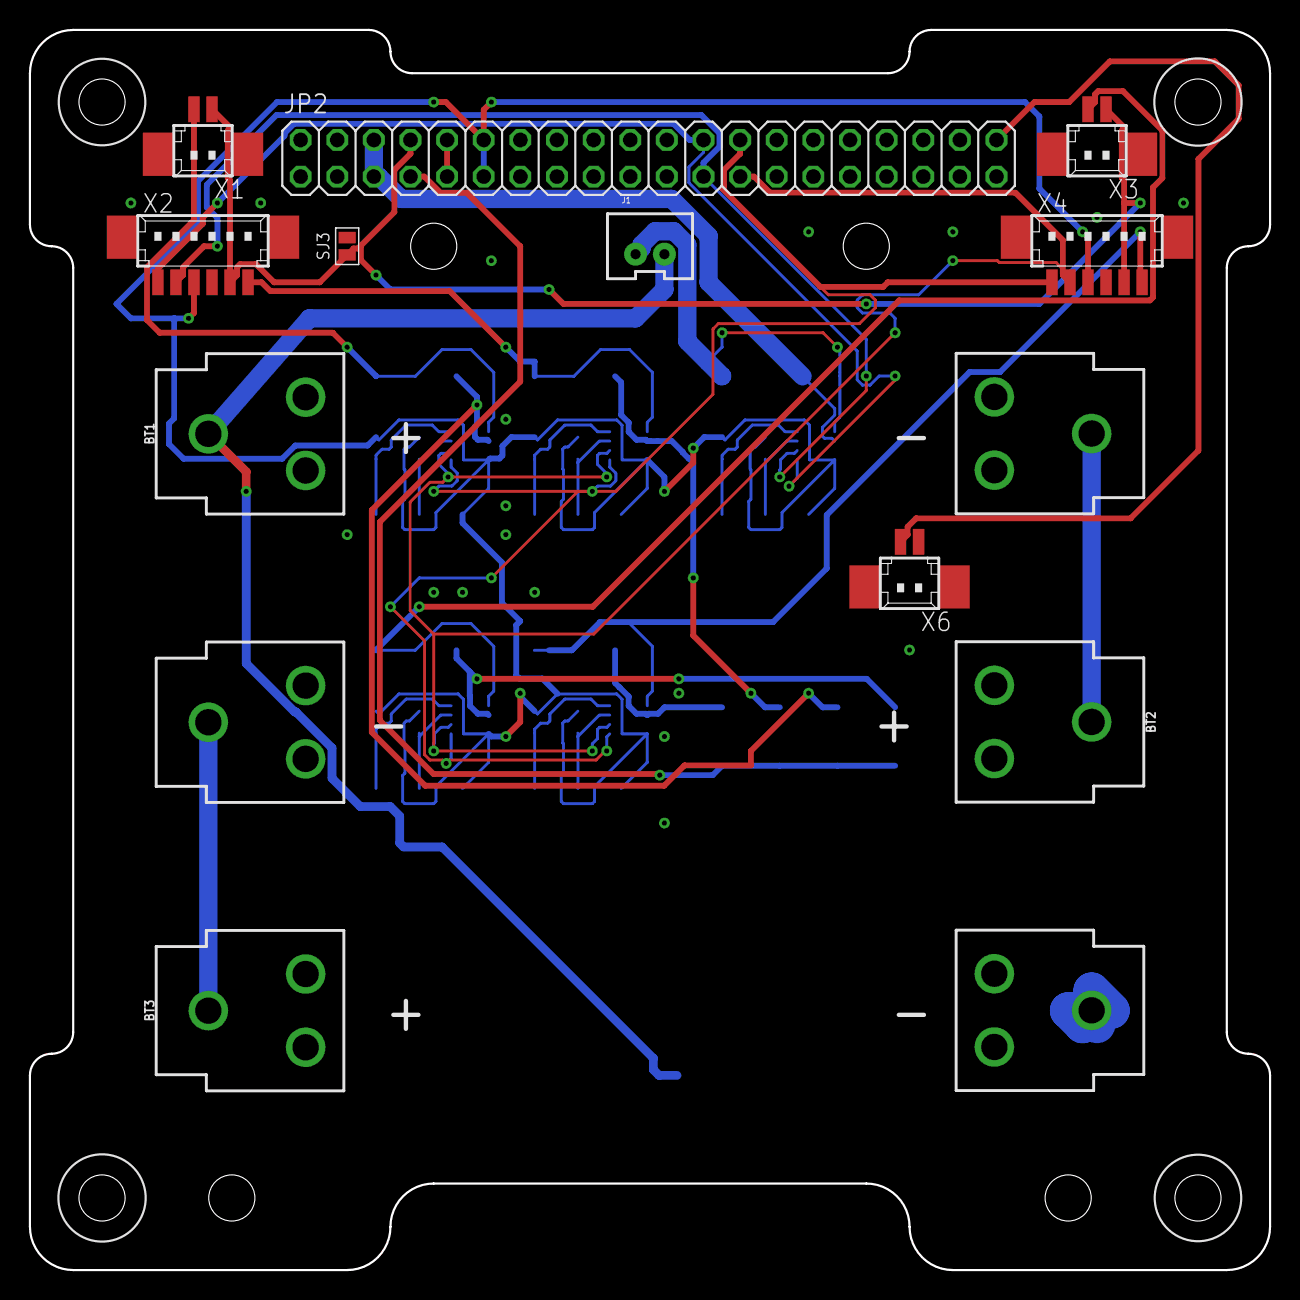
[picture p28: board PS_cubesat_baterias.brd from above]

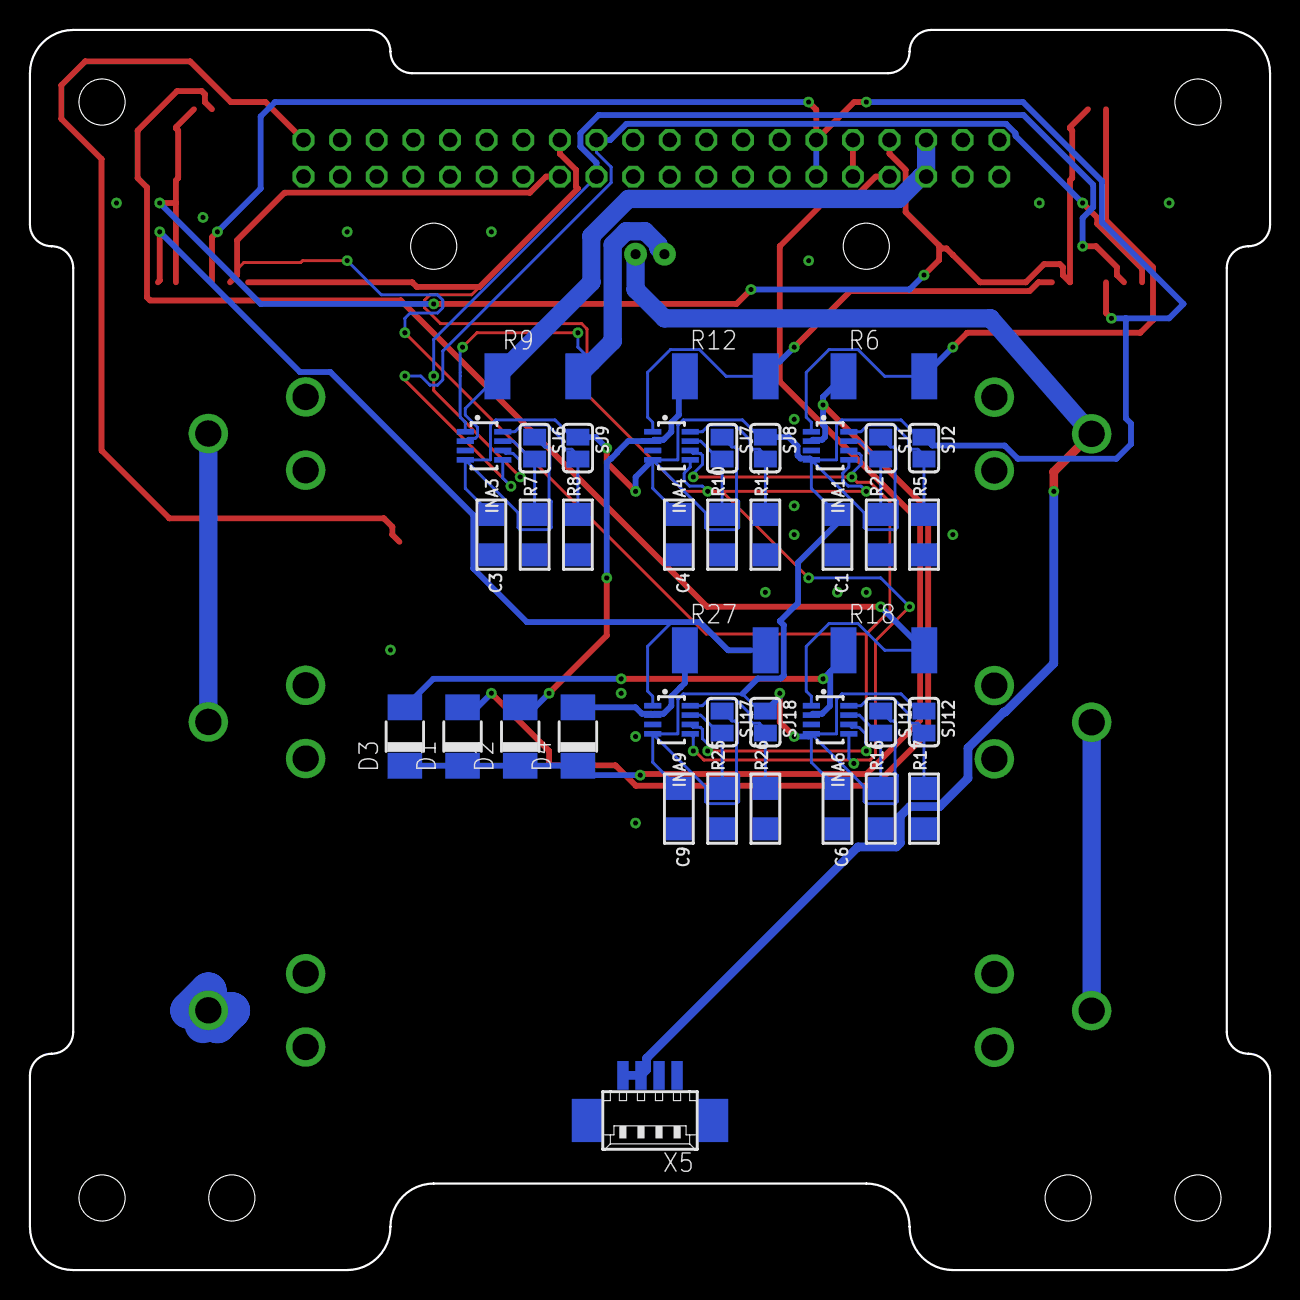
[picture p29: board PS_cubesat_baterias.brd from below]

Board: 2 copper layers, 86.0 x 86.0 mm, 51 parts (40 on the bottom side), 33 nets.

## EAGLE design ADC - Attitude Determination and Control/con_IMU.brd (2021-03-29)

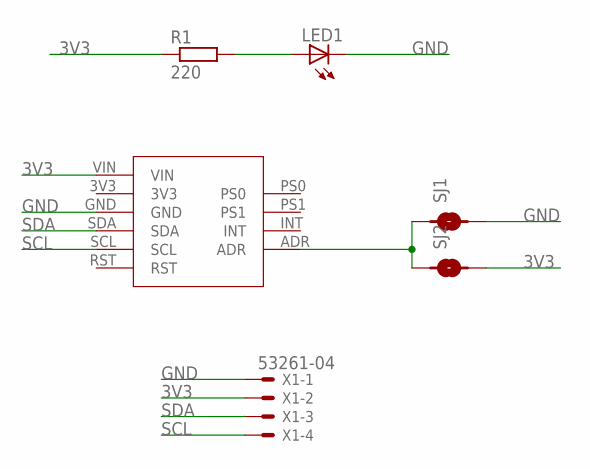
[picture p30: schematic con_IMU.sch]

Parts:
LED1: LEDCHIPLED_1206; CHIPLED_1206
R1: 220; R1206
SJ1, SJ2: SMD-JUMPER-2
U$1: BNO055; BNO055_MOD
X1: 53261-04

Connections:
3V3: R1.1, SJ2.2, U$1.VIN, X1.2
GND: LED1.C, SJ1.2, U$1.GND, X1.1
unnamed: LED1.A, R1.2
unnamed: SJ1.1, SJ2.1, U$1.ADR
SCL: U$1.SCL, X1.4
SDA: U$1.SDA, X1.3

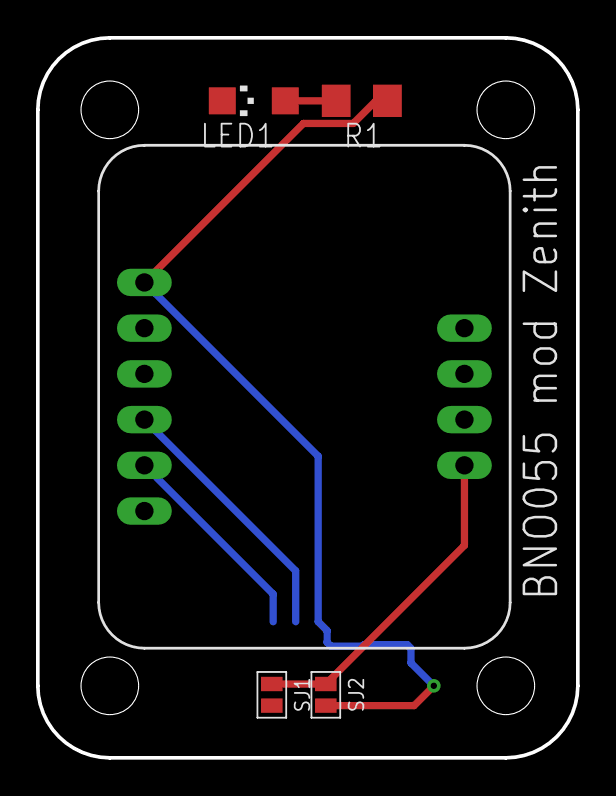
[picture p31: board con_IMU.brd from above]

Board: 2 copper layers, 30.0 x 40.0 mm, 6 parts (1 on the bottom side), 6 nets.

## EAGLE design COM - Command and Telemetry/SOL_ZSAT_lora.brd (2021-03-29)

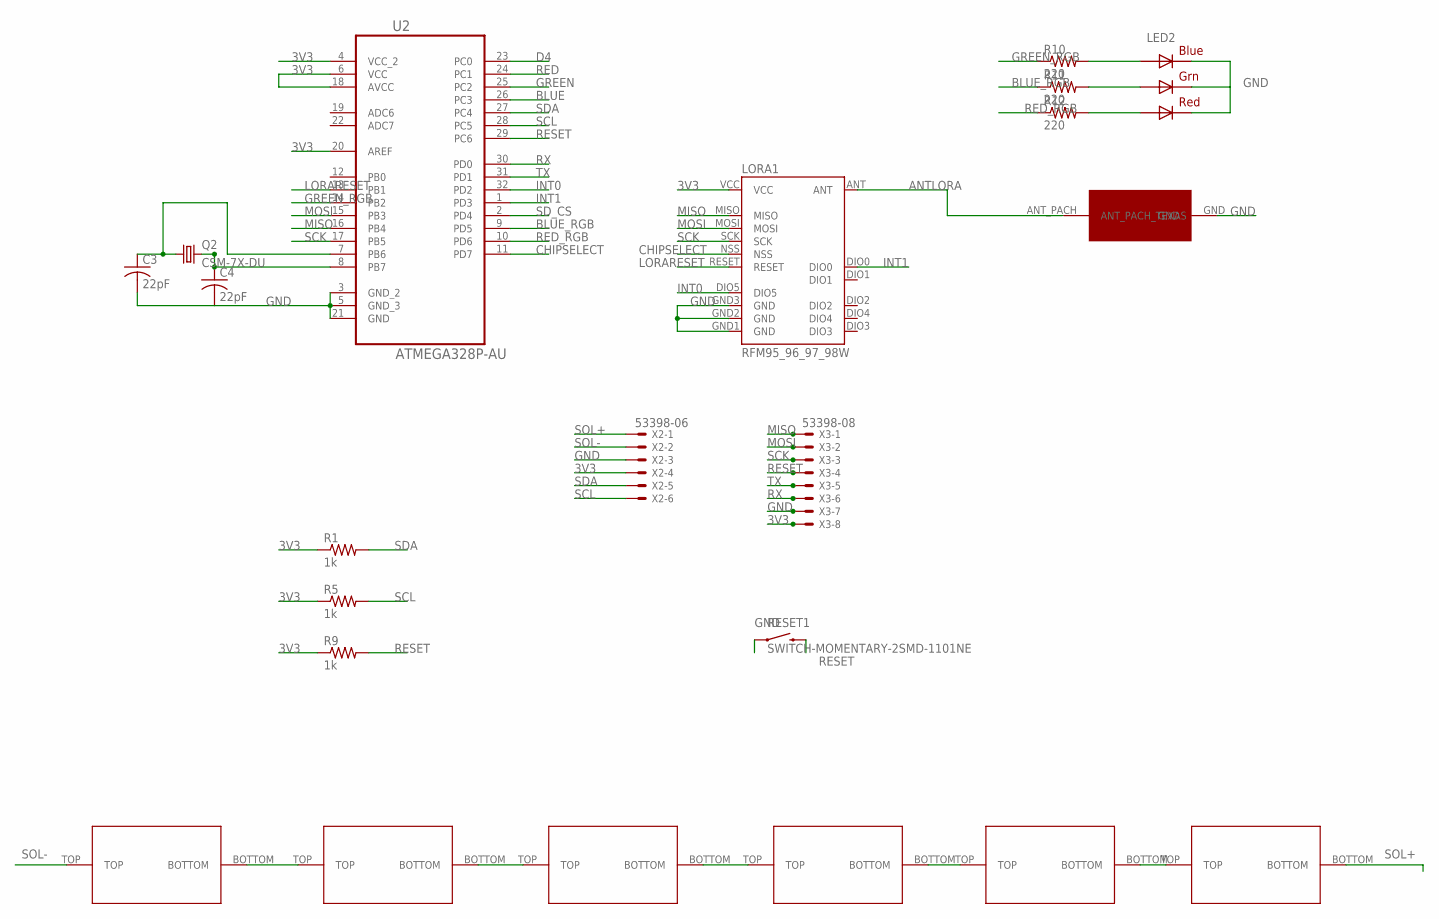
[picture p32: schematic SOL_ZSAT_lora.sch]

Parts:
C3, C4: 22pF; C0603
LED2: RGBLED5050
LORA1: RFM95_96_97_98W
Q2: CSM-7X-DU
R1, R5, R9: 1k; M1206
R10, R11, R12: 220; R0603
RESET1: SWITCH-MOMENTARY-2SMD-1101NE; TACTILE-SWITCH-1101NE
U2: ATMEGA328P-AU; QFP80P900X900X120-32N
U$1, U$2, U$3, U$4, U$5, U$6: SOL_26X52; SOLAR_52X26
U$7: 915MHZ_PACH_TEXAS
X2: 53398-06
X3: 53398-08

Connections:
3V3: LORA1.VCC, R1.1, R5.1, R9.1, U2.4 (VCC_2), U2.6 (VCC), U2.18 (AVCC), U2.20 (AREF), X2.4, X3.8
ANTLORA: LORA1.ANT, U$7.ANT_PACH (ANT_PACH_TEXAS)
BLUE: U2.26 (PC3)
BLUE_RGB: R11.1, U2.9 (PD5)
CHIPSELECT: LORA1.NSS, U2.11 (PD7)
D4: U2.23 (PC0)
GND: C3.2, C4.2, LED2.4 (BLUE_C), LED2.5 (RED_C), LED2.6 (GREEN_C), LORA1.GND1 (GND), LORA1.GND2 (GND), LORA1.GND3 (GND), RESET1.1, U2.3 (GND_2), U2.5 (GND_3), U2.21 (GND), U$7.GND, X2.3, X3.7
GREEN: U2.25 (PC2)
GREEN_RGB: R10.1, U2.14 (PB2)
INT0: LORA1.DIO5, U2.32 (PD2)
INT1: LORA1.DIO0, U2.1 (PD3)
LORARESET: LORA1.RESET, U2.13 (PB1)
MISO: LORA1.MISO, U2.16 (PB4), X3.1
MOSI: LORA1.MOSI, U2.15 (PB3), X3.2
unnamed: U$1.BOTTOM, U$2.TOP
unnamed: U$2.BOTTOM, U$3.TOP
unnamed: U$3.BOTTOM, U$4.TOP
unnamed: U$4.BOTTOM, U$5.TOP
unnamed: U$5.BOTTOM, U$6.TOP
unnamed: C4.1, Q2.2, U2.8 (PB7)
unnamed: C3.1, Q2.1, U2.7 (PB6)
unnamed: LED2.3 (BLUE_A), R10.2
unnamed: LED2.1 (GREEN_A), R11.2
unnamed: LED2.2 (RED_A), R12.2
RED: U2.24 (PC1)
RED_RGB: R12.1, U2.10 (PD6)
RESET: R9.2, RESET1.2, U2.29 (PC6), X3.4
RX: U2.30 (PD0), X3.6
SCK: LORA1.SCK, U2.17 (PB5), X3.3
SCL: R5.2, U2.28 (PC5), X2.6
SDA: R1.2, U2.27 (PC4), X2.5
SD_CS: U2.2 (PD4)
SOL+: U$6.BOTTOM, X2.1
SOL-: U$1.TOP, X2.2
TX: U2.31 (PD1), X3.5

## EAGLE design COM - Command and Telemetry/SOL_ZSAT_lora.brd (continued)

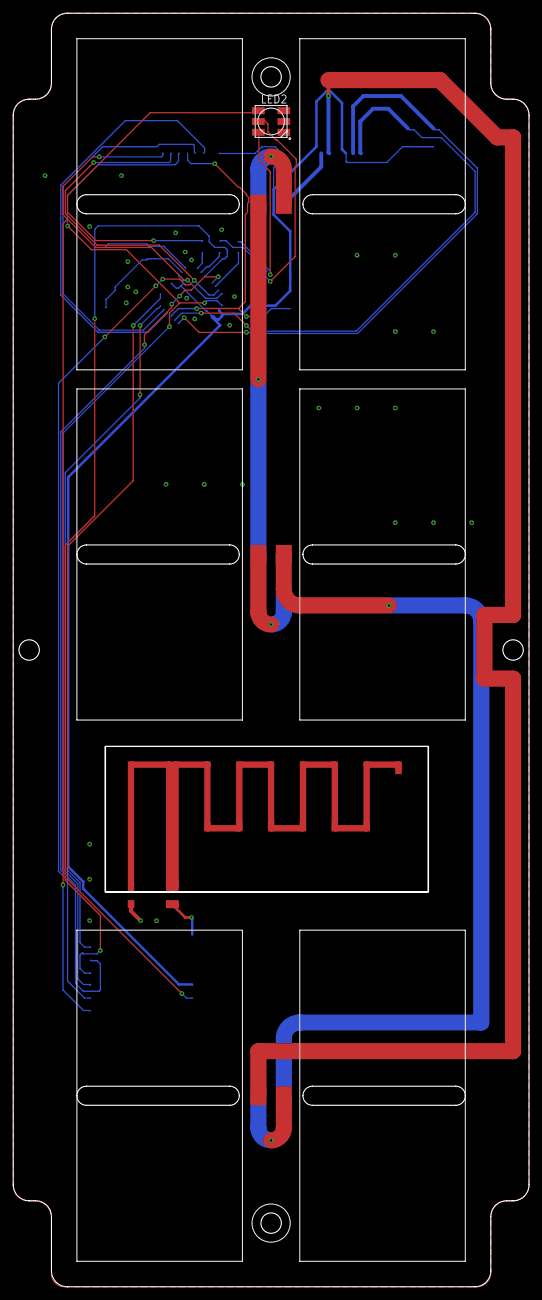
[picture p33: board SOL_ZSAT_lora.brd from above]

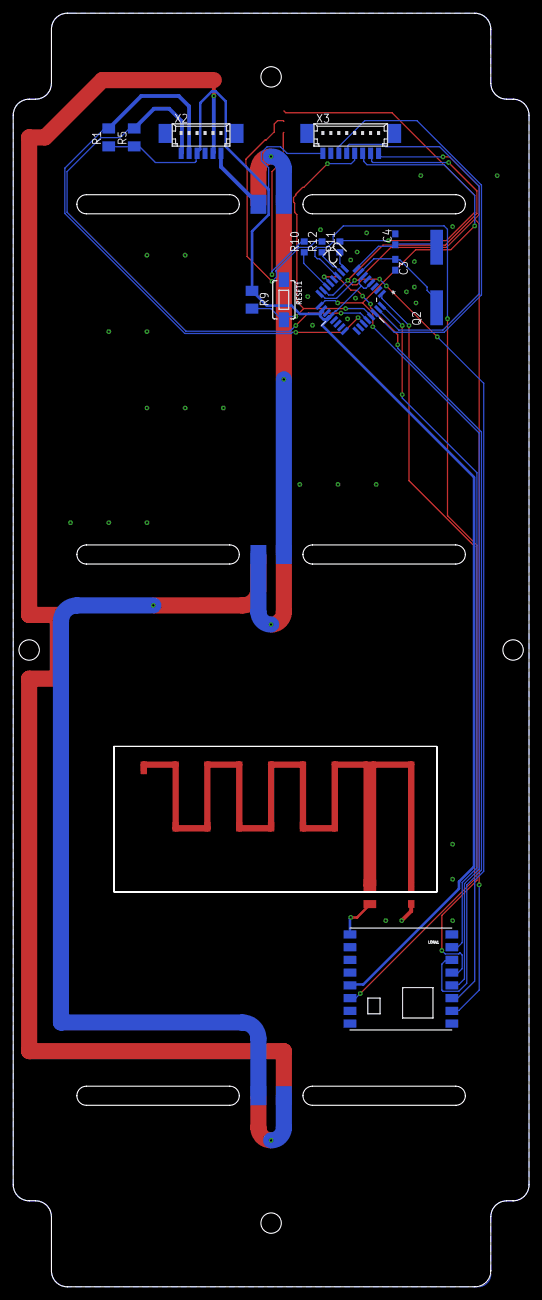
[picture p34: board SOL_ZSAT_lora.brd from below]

Board: 2 copper layers, 81.0 x 200.0 mm, 22 parts (14 on the bottom side), 30 nets.

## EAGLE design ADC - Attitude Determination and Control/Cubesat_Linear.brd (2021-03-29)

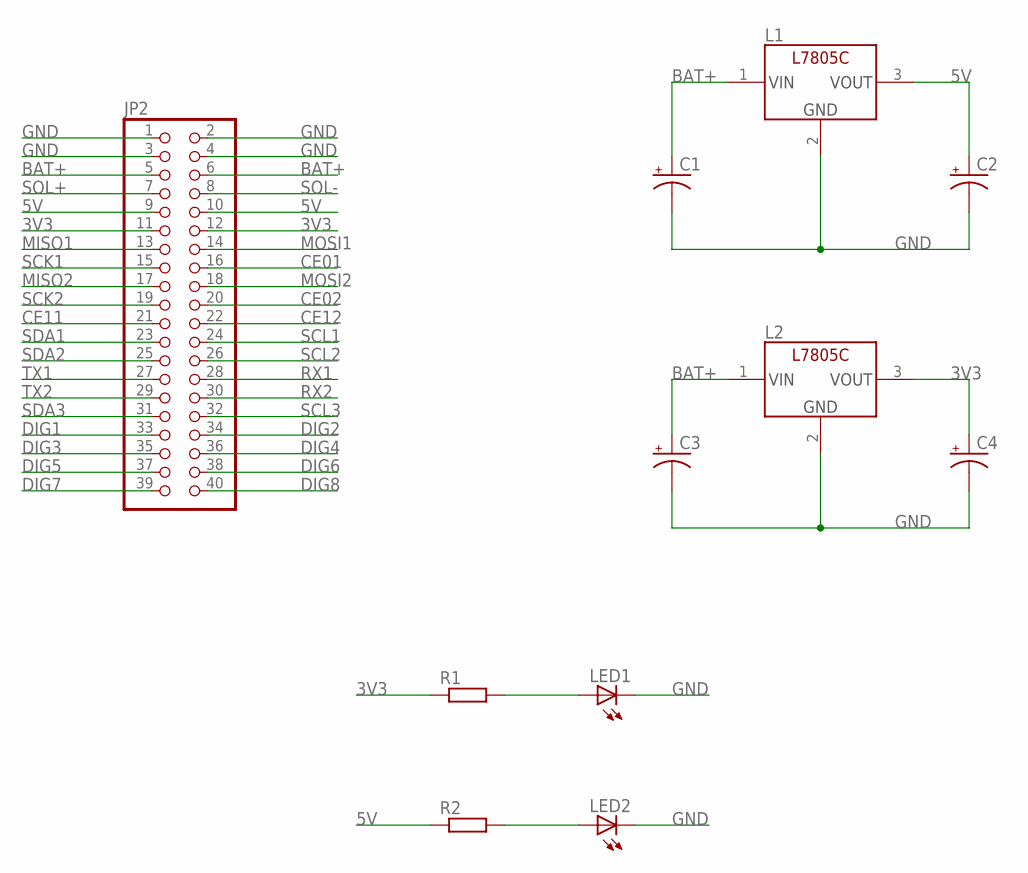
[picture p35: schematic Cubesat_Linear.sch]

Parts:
C1, C2, C3, C4: CAP_POLC; PANASONIC_C
JP2: PINHD-2X20; 2X20
L1, L2: L7805C; TO-220
LED1, LED2: LEDCHIPLED_1206; CHIPLED_1206
R1, R2: RR1206; R1206

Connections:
3V3: C4.+, JP2.11, JP2.12, L2.3 (VOUT), R1.1
5V: C2.+, JP2.9, JP2.10, L1.3 (VOUT), R2.1
BAT+: C1.+, C3.+, JP2.5, JP2.6, L1.1 (VIN), L2.1 (VIN)
CE01: JP2.16
CE02: JP2.20
CE11: JP2.21
CE12: JP2.22
DIG1: JP2.33
DIG2: JP2.34
DIG3: JP2.35
DIG4: JP2.36
DIG5: JP2.37
DIG6: JP2.38
DIG7: JP2.39
DIG8: JP2.40
GND: C1.-, C2.-, C3.-, C4.-, JP2.1, JP2.2, JP2.3, JP2.4, L1.2 (GND), L2.2 (GND), LED1.C, LED2.C
MISO1: JP2.13
MISO2: JP2.17
MOSI1: JP2.14
MOSI2: JP2.18
unnamed: LED1.A, R1.2
unnamed: LED2.A, R2.2
RX1: JP2.28
RX2: JP2.30
SCK1: JP2.15
SCK2: JP2.19
SCL1: JP2.24
SCL2: JP2.26
SCL3: JP2.32
SDA1: JP2.23
SDA2: JP2.25
SDA3: JP2.31
SOL+: JP2.7
SOL-: JP2.8
TX1: JP2.27
TX2: JP2.29


Board: 2 copper layers, 86.0 x 86.0 mm, 11 parts (0 on the bottom side), 6 nets.

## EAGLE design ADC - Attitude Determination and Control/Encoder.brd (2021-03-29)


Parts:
C1, C2: 22pF; C0603
C3: CC1206; C1206
LED1: LEDCHIPLED_1206; CHIPLED_1206
LED4: RGBLED5050
OS1: TCRT5000
Q1: CSM-7X-DU
R1, R3: R-US_M1206; M1206
R2, R4, R5, R6, R7: 220; R0603
RESET2: SWITCH-MOMENTARY-2SMD-1101NE; TACTILE-SWITCH-1101NE
U1: ATMEGA328P-AU; QFP80P900X900X120-32N
X1: 53261-08
X2: 53398-04

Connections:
3V3: C3.1, R1.1, R2.1, R3.1, R7.2, U1.4 (VCC_2), U1.6 (VCC), U1.18 (AVCC), U1.20 (AREF), X1.8, X2.3
BLUE_RGB: R5.1, U1.26 (PC3)
CE11: U1.14 (PB2)
D4_AT: U1.23 (PC0)
DI1_1_AT: U1.2 (PD4)
DIR_2_AT: U1.11 (PD7)
DIR_3_AT: U1.12 (PB0)
ENCODER: OS1.C (COLLECTOR), R7.1, U1.25 (PC2)
GND: C1.2, C2.2, C3.2, LED1.C, LED4.4 (BLUE_C), LED4.5 (RED_C), LED4.6 (GREEN_C), OS1.E (EMITTER), OS1.K (CATHODE), RESET2.1, U1.3 (GND_2), U1.5 (GND_3), U1.21 (GND), X1.7, X2.4
GREEN_RGB: R4.1, U1.13 (PB1)
INT0: U1.32 (PD2)
MISO1: U1.16 (PB4), X1.1
MOSI1: U1.15 (PB3), X1.2
unnamed: C2.1, Q1.2, U1.8 (PB7)
unnamed: C1.1, Q1.1, U1.7 (PB6)
unnamed: LED4.3 (BLUE_A), R4.2
unnamed: LED4.1 (GREEN_A), R5.2
unnamed: OS1.A (ANODE), R2.2
unnamed: LED1.A, R3.2
unnamed: LED4.2 (RED_A), R6.2
RED: U1.24 (PC1)
RED_RGB: R6.1, U1.10 (PD6)
RESET: R1.2, RESET2.2, U1.29 (PC6), X1.4
RX: U1.30 (PD0), X1.6
SCK1: U1.17 (PB5), X1.3
SCL3: U1.28 (PC5), X2.1
SDA3: U1.27 (PC4), X2.2
SP_1: U1.9 (PD5)
SP_3: U1.1 (PD3)
TX: U1.31 (PD1), X1.5



Board: 2 copper layers, 86.0 x 86.0 mm, 18 parts (2 on the bottom side), 21 nets.

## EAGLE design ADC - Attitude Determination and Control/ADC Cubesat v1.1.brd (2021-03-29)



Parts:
C1: 100nf; C1206
C2, C3, C4: 4.3pf; C1206
C5, C6, C9, C10, C11, C12: 0.1uf; C1210
C7: 100uf; PANASONIC_C
C8, C19: 10uF; C1206
C13, C14: 22pF; C0603
C15, C16: 22pF; 0805-NO
C17: 0.1uF; 0805-NO
C18: 0.1uF; 0805_10MGAP
D1, D3, D4: ss54; DO-214AC
IC1, IC4, IC5: DRV11873PWPR; SOP65P640X120-17N
J1: M04JST-PTH-VERT; JST-4-PTH-VERT
JP2: PINHD-2X20; 2X20
LED1, LED3: LEDSML1206; SML1206
LED2: RGBLED5050
Q2: CSM-7X-DU
R1: RR1206; R1206
R2, R3, R4, R5, R6, R12, R13, R14, R15, R16, R17, R18, R19, R20, R21: 1K; R1206
R7: 1k; R1206
R8: 220; R1206
R11, R22, R23, R24: 10K; 0805-NO
R29: R-US_M1206; M1206
R30, R31, R32: 220; R0603
RESET1: SWITCH-MOMENTARY-2SMD-1101NE; TACTILE-SWITCH-1101NE
S1: .; TACTILE-SWITCH-1101NE
SJ1, SJ2, SJ3, SJ4, SJ5, SJ6, SJ7, SJ8, SJ9: SMD-JUMPER-2
U1: STM32L476RGT6; LQFP64_10X10
U3: ATMEGA328P-AU; QFP80P900X900X120-32N
U$3: BNO055
X1: 53261-12
X2, X6: 53261-04
X4: 53261-08
X5, X7, X8: JST-XH-03-PIN-ROUND-PAD; JST-XH-03-PACKAGE-ROUND-PAD
Y1, Y2: 32.768kHz; CRYSTAL_8X3.8

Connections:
3V3: C4.2, C8.1, C18.2, C19.1, JP2.11, JP2.12, R3.2, R8.2, R12.2, R17.2, R24.2, R29.1, U1.1 (VBAT), U1.13 (VDDA/VREF_PLUS), U1.19 (VDD), U1.32 (VDD), U1.48 (VDDUSB), U1.64 (VDD), U3.4 (VCC_2), U3.6 (VCC), U3.18 (AVCC), U3.20 (AREF), U$3.3 (VDD), U$3.4 (NBOOT_LOAD_PIN), U$3.28 (VDDIO), X1.3, X2.2, X4.8, X6.2
5V: JP2.9, JP2.10
A2: U1.20 (PA4)
A3: U1.26 (PB0)
A4: U1.9 (PC1)
A5: U1.8 (PC0)
BAT+: C7.+, D1.A, D3.A, D4.A, J1.4, JP2.5, JP2.6, R7.2
BAT+RTF1: C5.2, D1.C, IC1.11 (VCC)
BAT+RTF2: C9.2, D3.C, IC4.11 (VCC)
BAT+RTF3: C11.2, D4.C, IC5.11 (VCC)
BLUE_RGB: R31.1, U3.26 (PC3)
BOOT0: R1.2, U1.60 (BOOT0), X1.6
CE01: JP2.16, U1.58 (PB6)
CE02: JP2.20
CE11: JP2.21, U3.14 (PB2)
CE12: JP2.22
COM1: IC1.13 (COM), R2.2, R4.2, R5.2
COM2: IC4.13 (COM), R14.2, R15.2, R16.2
COM3: IC5.13 (COM), R19.2, R20.2, R21.2
CPN1: C6.1, IC1.6 (CPN)
CPN2: C10.1, IC4.6 (CPN)
CPN3: C12.1, IC5.6 (CPN)
CPP1: C6.2, IC1.5 (CPP)
CPP3: C12.2, IC5.5 (CPP)
CPP12: C10.2, IC4.5 (CPP)
CS1: IC1.14 (CS), R6.2
CS2: IC4.14 (CS), R13.2
CS3: IC5.14 (CS), R18.2
D4_AT: U3.23 (PC0)
D7: U1.41 (PA8)
DI1_1_AT: U3.2 (PD4)
DIG1: JP2.33, SJ7.2
DIG2: JP2.34
DIG3: JP2.35
DIG4: JP2.36
DIG5: JP2.37
DIG6: JP2.38
DIG7: JP2.39
DIG8: JP2.40
DIR1: IC1.15 (FR), SJ2.1, SJ8.1, U1.42 (PA9)
DIR2: IC4.15 (FR), SJ4.1, U1.57 (PB5)
DIR3: IC5.15 (FR), SJ6.1, U1.43 (PA10)
DIR_1_AT: SJ2.2
DIR_2_AT: SJ4.2, U3.11 (PD7)
DIR_3_AT: SJ6.2, U3.12 (PB0)
GND: C1.1, C2.1, C3.1, C4.1, C7.-, C8.2, C13.2, C14.2, C15.1, C16.1, C17.1, C18.1, C19.2, IC1.8 (GND), IC4.8 (GND), IC5.8 (GND), J1.3, JP2.1, JP2.2, JP2.3, JP2.4, LED1.C, LED2.4 (BLUE_C), LED2.5 (RED_C), LED2.6 (GREEN_C), LED3.C, R1.1, R6.1, R11.2, R13.1, R18.1, R22.2, RESET1.1, S1.1, U1.12 (VSSA/VREF_MINUS), U1.18 (VSS), U1.31 (VSS), U1.47 (VSS), U1.63 (VSS), U3.3 (GND_2), U3.5 (GND_3), U3.21 (GND), U$3.2 (GND), U$3.10 (PIN10(GND)), U$3.15 (PIN15(GND)), U$3.16 (PIN16(GND)), U$3.18 (COM2(GND)), U$3.25 (GND), X1.4, X2.1, X4.7, X6.1
GREEN_RGB: R30.1, U3.25 (PC2)
I2CADDR_3V: R23.1, U$3.17 (COM3/I2C_ADDR)
INT0: U3.32 (PD2)
INT_3V: U$3.14 (INT)
MCO: U1.5 (PH0-OSC-IN), X1.7
MISO1: JP2.13, U1.22 (PA6), U3.16 (PB4), X4.1
MISO2: JP2.17
MOSI1: JP2.14, U1.23 (PA7), U3.15 (PB3), X4.2
MOSI2: JP2.18
unnamed: C3.2, U1.3 (PC14-OSC32-IN), Y1.P$4 (2)
unnamed: J1.1, SJ8.2
unnamed: C2.2, U1.4 (PC15-OSC32-OUT), Y1.P$1 (1)
unnamed: J1.2, SJ9.2
unnamed: LED1.A, R7.1
unnamed: C14.1, Q2.2, U3.8 (PB7)
unnamed: C15.2, U$3.27 (XIN32), Y2.P$4 (2)
unnamed: C16.2, U$3.26 (XOUT32), Y2.P$1 (1)
unnamed: C17.2, U$3.9 (CAP)
unnamed: C13.1, Q2.1, U3.7 (PB6)
unnamed: LED2.3 (BLUE_A), R30.2
unnamed: LED2.1 (GREEN_A), R31.2
unnamed: LED2.2 (RED_A), R32.2
unnamed: LED3.A, R8.1
NRESET_3V: R24.1, U$3.11 (NRESET)
NRST: C1.2, S1.2, SJ7.1, U1.7 (NRST), X1.8
PS0_3V: R11.1, U$3.6 (PS0)
PS1_3V: R22.1, U$3.5 (PS1)
PWM_SPEED1: IC1.16 (PWMIN), SJ3.1, SJ9.1, U1.38 (PC7)
PWM_SPEED2: IC4.16 (PWMIN), SJ1.1, U1.29 (PB10)
PWM_SPEED3: IC5.16 (PWMIN), SJ5.1, U1.56 (PB4)
RED: U3.24 (PC1)
RED_RGB: R32.1, U3.10 (PD6)
RESET: R29.2, RESET1.2, U3.29 (PC6), X4.4
RX: U3.30 (PD0), X4.6
RX1: JP2.28
RX2: JP2.30
SCK1: JP2.15, U1.21 (PA5), U3.17 (PB5), X4.3
SCK2: JP2.19
SCL1: JP2.24
SCL2: JP2.26
SCL3: JP2.32, U1.61 (PB8), U3.28 (PC5), U$3.19 (COM1/SCL/RX), X1.12, X2.4, X6.4
SDA1: JP2.23
SDA2: JP2.25
SDA3: JP2.31, U1.62 (PB9), U3.27 (PC4), U$3.20 (COM0/SDA/TX), X1.11, X2.3, X6.3
SET_TYPE: IC1.1 (FS), R3.1
SET_TYPE2: IC4.1 (FS), R12.1
SET_TYPE3: IC5.1 (FS), R17.1
SOL+: JP2.7
SOL-: JP2.8
SP_1: SJ3.2, U3.9 (PD5)
SP_2: SJ1.2, U3.13 (PB1)
SP_3: SJ5.2, U3.1 (PD3)
SWO: U1.55 (PB3), X1.5
TCK: U1.49 (PA14), X1.1
TMS: U1.46 (PA13), X1.2
TX: U3.31 (PD1), X4.5
TX1: JP2.27
TX2: JP2.29
U1: IC1.10 (U), R5.1, X5.2
U2: IC4.10 (U), R16.1, X7.2
U3: IC5.10 (U), R21.1, X8.2
USART_RX: U1.17 (PA3), X1.9
USART_TX: U1.16 (PA2), X1.10
V1: IC1.9 (V), R4.1, X5.3
V2: IC4.9 (V), R15.1, X7.3
V3: IC5.9 (V), R20.1, X8.3
VCP1: C5.1, IC1.4 (VCP)
VCP2: C9.1, IC4.4 (VCP)
VCP3: C11.1, IC5.4 (VCP)
W1: IC1.7 (W), R2.1, X5.1
W2: IC4.7 (W), R14.1, X7.1
W3: IC5.7 (W), R19.1, X8.1



Board: 2 copper layers, 86.0 x 86.0 mm, 80 parts (12 on the bottom side), 85 nets.

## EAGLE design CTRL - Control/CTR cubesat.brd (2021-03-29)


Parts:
JP2: PINHD-2X20; 2X20
SJ1, SJ2, SJ3, SJ4, SJ5, SJ6: SMD-JUMPER-2
U$1, U$2: RASPBERRY-PI+PIZERO; RASPBERRY-PI-ZERO

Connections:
3V3: JP2.11, JP2.12, SJ1.1, SJ2.1
5V: JP2.9, JP2.10, U$1.2 (2-5V), U$1.4 (4-5V), U$2.2 (2-5V), U$2.4 (4-5V)
BAT+: JP2.5, JP2.6
CE01: JP2.16, U$2.24 (24-GPIO8)
CE02: JP2.20, U$1.24 (24-GPIO8)
CE11: JP2.21, U$2.26 (26-GPIO7)
CE12: JP2.22, U$1.26 (26-GPIO7)
DIG1: JP2.33, U$2.7 (7-GPIO4)
DIG2: JP2.34, SJ3.1
DIG3: JP2.35, SJ4.1
DIG4: JP2.36, SJ5.1
DIG5: JP2.37, SJ6.1
DIG6: JP2.38
DIG7: JP2.39
DIG8: JP2.40
GND: JP2.1, JP2.2, JP2.3, JP2.4, U$1.6 (6-GND), U$1.9 (9-GND), U$1.14 (14-GND), U$1.20 (20-GND), U$1.25 (25-GND), U$1.30 (30-GND), U$1.34 (34-GND), U$1.39 (39-GND), U$2.6 (6-GND), U$2.9 (9-GND), U$2.14 (14-GND), U$2.20 (20-GND), U$2.25 (25-GND), U$2.30 (30-GND), U$2.34 (34-GND), U$2.39 (39-GND)
MISO1: JP2.13, U$2.21 (21-SPI-MISO/GPIO9)
MISO2: JP2.17, U$1.21 (21-SPI-MISO/GPIO9)
MOSI1: JP2.14, U$2.19 (19-SPI-MOSI/GPIO10)
MOSI2: JP2.18, U$1.19 (19-SPI-MOSI/GPIO10)
unnamed: SJ1.2, U$2.1 (1-3V3)
unnamed: SJ2.2, U$1.1 (1-3V3)
unnamed: SJ3.2, U$2.11 (11-GPIO17)
unnamed: SJ4.2, U$2.13 (13-GPIO27)
unnamed: SJ5.2, U$1.11 (11-GPIO17)
unnamed: SJ6.2, U$1.13 (13-GPIO27)
RX1: JP2.28, U$1.8 (8-TX), U$2.10 (10-RX)
RX2: JP2.30
SCK1: JP2.15, U$2.23 (23-SPI-SCLK/GPIO11)
SCK2: JP2.19, U$1.23 (23-SPI-SCLK/GPIO11)
SCL1: JP2.24, U$2.5 (5-SCL1/GPIO3)
SCL2: JP2.26, U$1.5 (5-SCL1/GPIO3)
SCL3: JP2.32
SDA1: JP2.23, U$2.3 (3-SDA1/GPIO2)
SDA2: JP2.25, U$1.3 (3-SDA1/GPIO2)
SDA3: JP2.31
SOL+: JP2.7
SOL-: JP2.8
TX1: JP2.27, U$1.10 (10-RX), U$2.8 (8-TX)
TX2: JP2.29

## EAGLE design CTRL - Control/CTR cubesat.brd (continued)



Board: 2 copper layers, 86.0 x 86.0 mm, 9 parts (6 on the bottom side), 31 nets.

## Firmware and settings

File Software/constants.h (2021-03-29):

/* * * * * * * * * * * * * * * * * * * * * * * * * * * * * * * * * * * * * * * * * *
 * ZenSat v1.0 - CubeSat                                                           *
 * Authors: João Matheus Siqueira Souza      (jmssouza)                            *
 *          Orlando Wozniak de Lima Nogueira (orlandowzk97)                        *
 *          Vinicius Eiji Sasaki             (sasakivinicius)                      *
 * São Carlos School of Engineering - University of São Paulo                      *
 * First semester - 2018                                                           *
 * * * * * * * * * * * * * * * * * * * * * * * * * * * * * * * * * * * * * * * * * */

#ifndef CODE_CONSTANTS_H
#define CODE_CONSTANTS_H

//Values constants
    #define PACK_SIZE  255
    #define BLOCK_SIZE 248
    #define PASSWORD   0000
    #define TIME_SIZE  21
    #define PS_SIZE    161
    #define ADC_SIZE   61



    #define ADD_I2C_ATMEGA  0x1 //TEM QUE ARRUMAR
    #define ADD_I2C_ATMEGA_BASE  0x2 //TEM QUE ARRUMAR
//SETAR ENDEREÇOS DOS INAS


    #define COD_VISAO       "VisaoCubeSat.py"
    #define PICTURE_NAME    "zenith.jpg"

//Files names
    #define CHECK_POWERED   "check_powered.dat"
    #define NEW_TM          "new_tm.dat"
    #define TM_FILE         "tm_file.dat"
    #define TM_NUMBER       "tm_num.dat"
    #define TM_CYCLE        "tm_cycle.dat"
    #define NEW_TC          "new_tc.dat"
    #define TC_FILE         "tc_file.dat"
    #define TC_NUMBER       "tc_num.dat"
    #define TC_CYCLE        "tc_cycle.dat"
    #define MISSED_PACKAGES "missed_packets.dat"
    #define MODE_FILE       "op_mode.dat"
    #define PS_FILE         "ps_file.dat"
    #define PS_NUMBER       "ps_num.dat"
    #define ADC_TX_FILE     "adc_tx_file.dat"
    #define ADC_TX_NUMBER   "adc_tx_num.dat"
    #define ADC_RX_FILE     "adc_rx_file.dat"
    #define ADC_RX_NUMBER   "adc_rx_num.dat"
    #define FILE_SLAVE      "adc_cv_slave.dat"
    #define FILE_MASTER     "adc_cv_master.dat"
    #define STD_LOOP        "std_loop.dat"
    #define PS_AUX          "ps_aux.dat"


//Backup files
    #define CHECK_POWERED_CP   "check_powered_cp.dat"
    #define NEW_TM_CP          "new_tm_cp.dat"
    #define TM_FILE_CP         "tm_file_cp.dat"
    #define TM_NUMBER_CP       "tm_num_cp.dat"
    #define TM_CYCLE_CP        "tm_cycle_cp.dat"
    #define NEW_TC_CP          "new_tc_cp.dat"
    #define TC_FILE_CP         "tc_file_cp.dat"
    #define TC_NUMBER_CP       "tc_num_cp.dat"
    #define TC_CYCLE_CP        "tc_cycle_cp.dat"
    #define MISSED_PACKAGES_CP "missed_packets_cp.dat"
    #define MODE_FILE_CP       "op_mode_cp.dat"
    #define PS_FILE_CP         "ps_file_cp.dat"
    #define PS_NUMBER_CP       "ps_num_cp.dat"
    #define ADC_TX_FILE_CP     "adc_tx_file_cp.dat"
    #define ADC_TX_NUMBER_CP   "adc_tx_num_cp.dat"
    #define ADC_RX_FILE_CP     "adc_rx_file_cp.dat"
    #define ADC_RX_NUMBER_CP   "adc_rx_num_cp.dat"
    #define FILE_SLAVE_CP      "adc_cv_slave_cp.dat"
    #define FILE_MASTER_CP     "adc_cv_master_cp.dat"
    #define STD_LOOP_CP        "std_loop_cp.dat
    #define PS_AUX_CP          "ps_aux_cp.dat"

#endif //CODE_CONSTANTS_H

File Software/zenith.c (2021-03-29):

/* * * * * * * * * * * * * * * * * * * * * * * * * * * * * * * * * * * * * * * * * *
 * ZenSat v1.0 - CubeSat                                                           *
 * Authors: João Matheus Siqueira Souza      (jmssouza)                            *
 *          Orlando Wozniak de Lima Nogueira (orlandowzk97)                        *
 *          Vinicius Eiji Sasaki             (sasakivinicius)                      *
 * São Carlos School of Engineering - University of São Paulo                      *
 * First semester - 2018                                                           *
 * * * * * * * * * * * * * * * * * * * * * * * * * * * * * * * * * * * * * * * * * */

#include "zenith.h"

//Files manipulation functions

int valueGetter(char *file_name, int *value){

    FILE *file;

    file = fopen(file_name, "r");
    if (file!=NULL){
        fscanf(file, "%d", value);
        fclose(file);
        return 1;
    }
    else{
        printf("ERROR - file %s cannot be opened", file_name);
        return 0;
    }
}

int valueSetter(char *file_name, int value){
    FILE *file;

    file = fopen(file_name, "w");
    if (file!=NULL){
        fprintf(file,"%d", value);
        fclose(file);
        return 1;
    }
    else{
        system("cls");
        printf("ERROR - file %s cannot be created", file_name);
        return 0;
    }
}

int writeMessage(char *file_name, char *message, int position, int size, int check){

    FILE *file;
    int i;

    file = fopen(file_name, "r+b");

    if (file != NULL){
        fseek(file, position*(size+check), SEEK_SET);
        fwrite(message, size, 1, file);
        fclose(file);
        return 1;
    }
    else{
        printf("Error - file %s cannot be opened.", file_name);
        return 0;
    }
}

int readMessage(char *file_name, char *message, int position, int size, int check){

    FILE *file;
    int i;

    for(i=0;i<size;i++){
        message[i]=0;
    }

    file = fopen(file_name, "r+b");

    if (file != NULL){
        fseek(file, position*(size+check), SEEK_SET);
        fread(message, size, 1, file);
        fclose(file);
        return 1;
    }
    else{
        printf("Error - file cannot be opened.");
        return 0;
    }
}




//General purpose functions

void delay(unsigned int micros){
    clock_t goal = micros + clock();
    while(goal>clock());
}

void reverse(char *str, int len){
    // reverses a string 'str' of length 'len'
    int i=0, j=len-1, temp;
    while (i<j)
    {
        temp = str[i];
        str[i] = str[j];
        str[j] = temp;
        i++; j--;
    }
}

int intToStr(int x, char str[], int d){
    // Converts a given integer x to string str[].  d is the number
    // of digits required in output. If d is more than the number
    // of digits in x, then 0s are added at the beginning.
    int i = 0;
    while (x)
    {
        str[i++] = (x%10) + '0';
        x = x/10;
    }

    // If number of digits required is more, then
    // add 0s at the beginning
    while (i < d)
        str[i++] = '0';

    reverse(str, i);
    str[i] = '\0';
    return i;
}

void ftoa(float n, char *res, int afterpoint){
    // Extract integer part
    int ipart = (int)n;

    // Extract floating part
    float fpart = n - (float)ipart;

    // convert integer part to string
    int i = intToStr(ipart, res, 0);

    // check for display option after point
    if (afterpoint != 0)
    {
        res[i] = '.';  // add dot

        // Get the value of fraction part upto given no.
        // of points after dot. The third parameter is needed
        // to handle cases like 233.007
        fpart = fpart * pow(10, afterpoint);

        intToStr((int)fpart, res + i + 1, afterpoint);
    }
}

int correctValue(int *values){
    if ((values[0]==values[1]) && (values[1]==values[2])){
        return values[0];
    }
    else if ((values[0]==values[1]) && (values[1]!=values[2])){
        return values[0];
    }
    else if ((values[0]!=values[1]) && (values[1]==values[2])){
        return  values[2];
    }
    else {
        return -1;
    }
}

void tenBlock(char *str){

    int size;
    int i = 0;

    size = strlen(str);

    if(size>=9){
        str[9] = ';';
        str[10] = '\0';
    }
    else if(size<9){
        for(i = 0; i< size; i++){ str[8-i] = str[size - (i+1)]; }
        for(i = 0; i< 9 - size; i++){ str[i] = '0'; }
        str[9]=';';
        str[10] = '\0';
    }
}

int headerInterface(){
    system("clear");
    printf("=========================================================================\n");
    printf("=                          CubeSat v1 - ZenSat                          =\n");
    printf("=========================================================================\n");
    return 0;
}

void getDate(char *time){
    time[0] = '\0';
    strcat(time,__DATE__);
    strcat(time, " ");
    strcat(time,__TIME__);
}




//Package manipulation functions
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

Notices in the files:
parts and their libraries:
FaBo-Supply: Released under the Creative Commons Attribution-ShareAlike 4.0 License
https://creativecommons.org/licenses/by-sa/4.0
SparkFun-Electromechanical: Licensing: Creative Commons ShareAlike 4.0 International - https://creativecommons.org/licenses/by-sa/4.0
